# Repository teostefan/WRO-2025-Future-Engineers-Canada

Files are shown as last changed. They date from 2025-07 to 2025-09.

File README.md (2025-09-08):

# WRO-2025-Future-Engineers-Canada

The following repository contains the code and technical documentation regarding
the robot created by the CarletonU-uOttawa joint team for the 2025 WRO Future
Engineers competition.

Robot Image

## Contents

- [About our Team](https://github.com/teostefan/WRO-2025-Future-Engineers-Canada/blob/main/README.md#about-our-team)
- [Demo Video](https://github.com/teostefan/WRO-2025-Future-Engineers-Canada/blob/main/README.md#demo-video)
- [Software Setup](https://github.com/teostefan/WRO-2025-Future-Engineers-Canada/blob/main/README.md#software-setup)
- [Power and Sensor Management](https://github.com/teostefan/WRO-2025-Future-Engineers-Canada/blob/main/README.md#power-and-sensor-management)
- [Obstacle Management](https://github.com/teostefan/WRO-2025-Future-Engineers-Canada/blob/main/README.md#obstacle-management)
- [Mobility Management](https://github.com/teostefan/WRO-2025-Future-Engineers-Canada/blob/main/README.md#mobility-management)

## About our Team

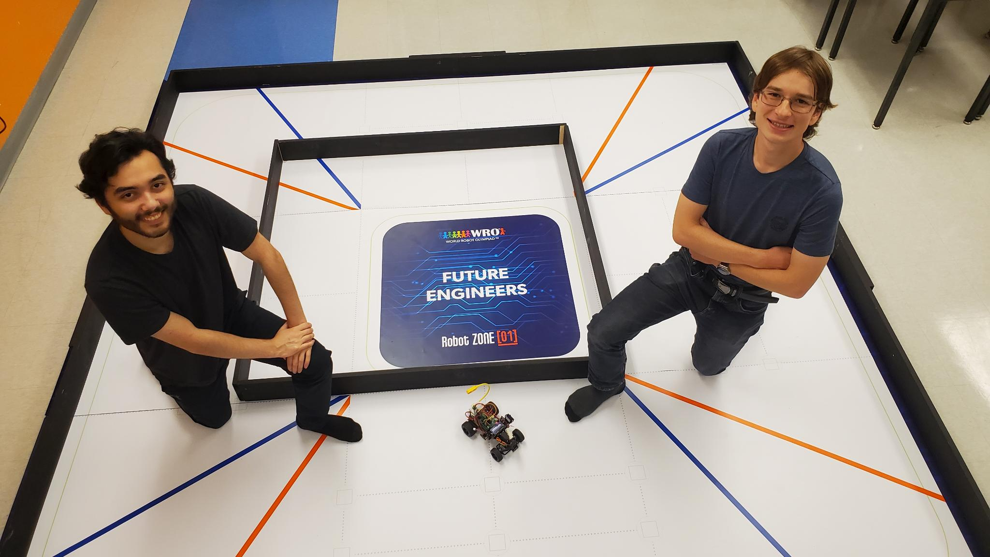
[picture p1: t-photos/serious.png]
Team Photo


Oscar Barbieri is a student at the University of Ottawa and is studying software engineering, and Stefan Teodorescu is a student a Carleton University studying aerospace avionics. Last year, Oscar and Stefan participated in the WRO Future Innovators challenge and made it into the international finals in İzmir. This year, both students have decided to participate in the WRO Future Engineers competition as a means to further their knowledge regarding mechatronics and systems programming.

## Demo Video

A demonstration video of our robot performing both challenges can be found in the [```video``` directory](https://github.com/teostefan/WRO-2025-Future-Engineers-Canada/tree/main/video).

## Software Setup

### Compiling and Running the Robot's Firmware (Linux)

To get started, clone the repository and build the firmware using `make`:

```sh
git clone https://github.com/teostefan/WRO-2025-Future-Engineers-Beta.git
cd WRO-2025-Future-Engineers-Beta
make
```

> **Note**: Depending on how your Linux system is configured, an "insufficient
> privileges" error may be thrown on compilation regarding the file
> `kf_matrix_gen.sh`. To solve this, run
> `sudo chmod 777 ./software/kf/kf_matrix_gen.sh` in the repository's root. If
> this error still persists, use `sudo` in front of `make` as your user might
> not have enough privileges to execute the above bash file.

Then, simply run the `main` executable in the generated `builds` folder:

```sh
builds/main
```

### Compiling and Running Individual Tests

To generate the test executables, run:

```sh
make all-tests
```

Afterwards, all tests will be in the `builds` folder and have a name in the
format `test_xx`. Each test can then be individually executed as in the
following example:

```sh
builds/test_cv
```

### Software Dependencies

If running on Linux, all of the below dependencies should be pre-installed.

- `ffmpeg` - Abstraction layer for the driver, also used for applying filters to
  the video feed.
- `v4l2` - Video4Linux2 multimedia drivers.
- `ffplay` - Media player GUI for debugging.
- `unistd.h` - The UNIX standard header.

## Power and Sensor Management

|Annotated Diagram|
|:--:|
|*Figure 1: Annotated diagram of the vehicle. Individual components are discussed in the subsequent sections.*|

This section pertains to the electrical engineering aspects of our vehicle. Design choices such as computing platforms, power supplies, sensors and motor controllers are discussed. The majority of peripherals have been purchased as breakout boards, and a custom Raspberry-P "Hat" acts as a distribution box and motor controller. A general block diagram of the robot's electrical systems is provided below.

|Drivetrain Diagram|
|:--:|
|*Figure 2: Diagram of the vehicle's electrical systems. Schematics regarding the custom Raspberry Pi Hat PCB and 5V converter for the servo are provided in the sections below.*|

### Computing Platform

The main controller for the robot is a Raspberry Pi 4B Single Board Computer (SBC). All processing is done on this platform, and no additional controllers have been used, except for an ATTINY45 that generates Pulse-Width Modulation (PWM) to control the speed on the driving motor. This ensures that the system remains simple and allows for a smaller vehicle, which implies better manoeuvrability. The Raspberry-Pi model 4B was specifically chosen as it has a good amount of processing capabilities for the computer-vision algorithms and does not excessively consume power like the newer model 5 (~2.5A@5V versus 5A@5V).

### Power Supply

The vehicle is powered by a 2Ah lithium-ion battery pack that feeds 7.4V nominal into a 3.4A fixed 5V buck regulator and a variable 2A buck-boost regulator set to approximately 9V. The 5V regulator supplies the Raspberry Pi, while the 9V regulator supplies the driving motor. As the steering servo requires 5V only, the 9V from the motor power supply is stepped down to 5V via a simple LM7805 linear regulator circuit (see Figure 3). Although the 5V could have been supplied from the main 5V regulator, this would have been undesirable as any electrical noise caused by the servomotor could permeate to the Raspberry Pi and cause instabilities. For supplying the sensors which work at 3.3V, the internal regulator on the Raspberry Pi is used.

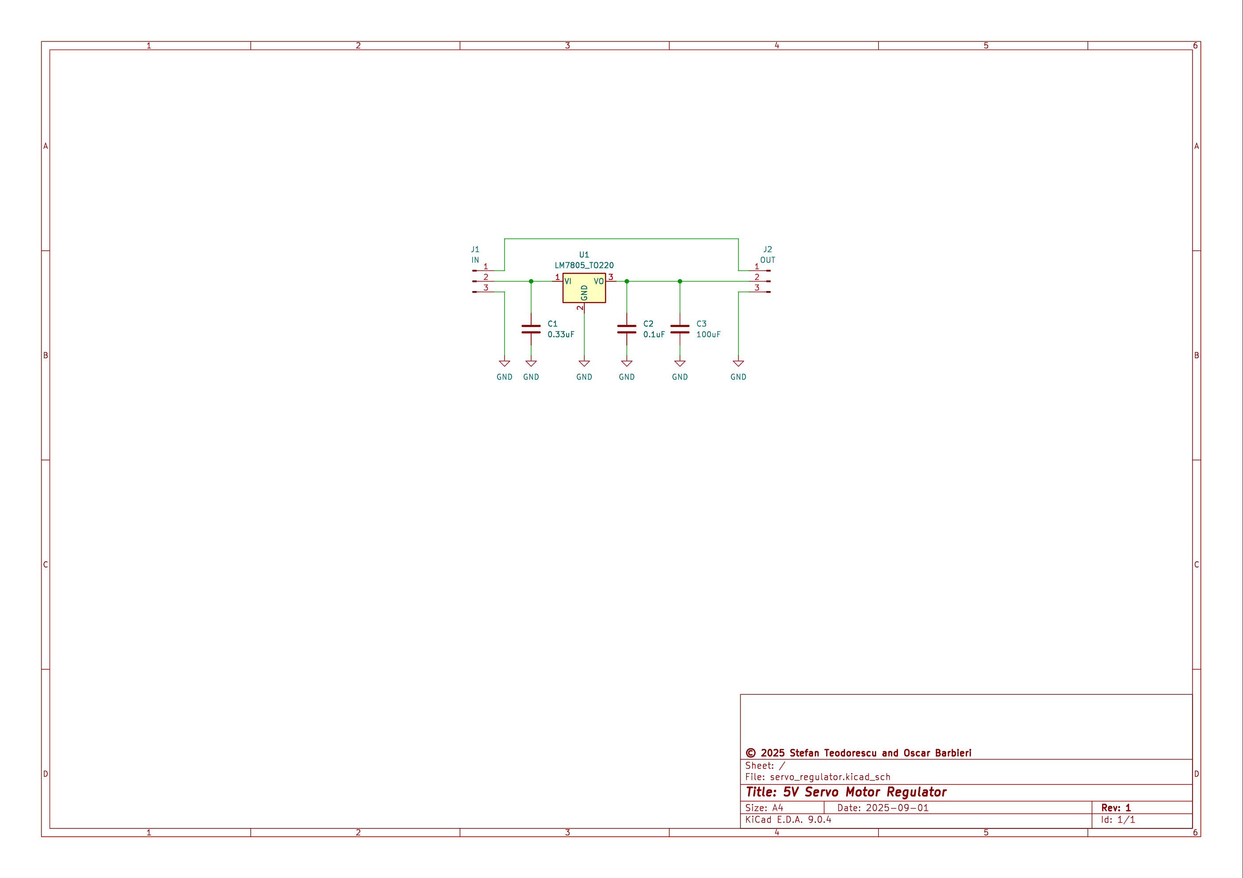
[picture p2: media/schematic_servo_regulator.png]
Servo Regulator Schematic
||
|:--:|
|*Figure 3: Schematic of the LM7805 5V regulator for the steering servo. Production files for this board can be found in the [`pcb/servo_regulator`](https://github.com/teostefan/WRO-2025-Future-Engineers-Canada/tree/main/pcb/servo_regulator) directory.*|

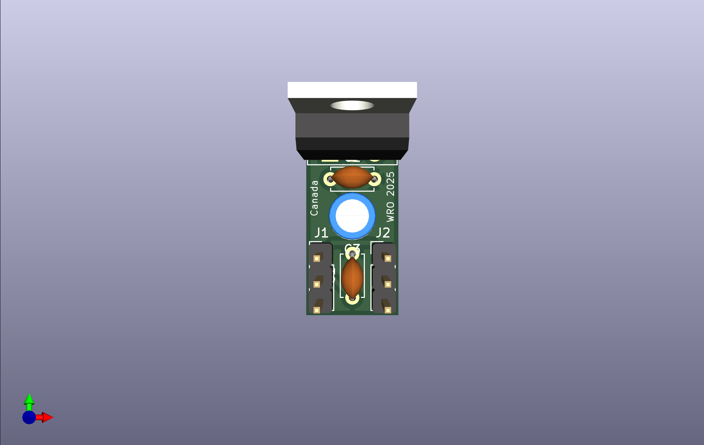
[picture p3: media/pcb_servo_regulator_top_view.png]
Servo Regulator Top View
||
|:--:|
|*Figure 4: Rendering of the servo regulator custom PCB in KiCAD.*|

### Sensor and Motor Management

In addition to the camera for obstacle detection, as many sensors as possible have been installed on the robot to simplify the control algorithms and to avoid estimating data. For example, all four sides of the robot have optical Time-of-Flight (ToF) distance sensors, allowing the vehicle not only to determine it's rectilinear position, but also to measure clearances precisely for manoeuvres such as parallel parking. In addition, a gyroscope has been installed which can measure absolute rotation angles of the robot. The gyro sensor is also used in a proportional controller to keep the robot driving straight when required.

All sensors, except for the camera which is connected via USB, are interfaced via a common I²C bus. To prevent conflicts in between sensors which have the same addresses (the 4 ToF sensors), an I²C-controlled multiplexer is used for connecting the main bus to only one sensor at a time.

Also on this main I²C bus is an ATTINY45 which is configured as a slave. It generates PWM signals that are then used to drive the DC driving motor via an H-bridge at varying speeds in forwards or reverse. The steering servomotor is separate and is controlled directly by the Raspberry Pi through PWM.

In order to reduce the number of external components and keep the wiring relatively manageable, a custom Raspberry Pi "Hat" has been designed. It includes connectors for all of the individual peripherals and integrates the driving motor controller as well as the I²C multiplexer. The circuit board was designed in KiCAD and all relevant files can be found in the `pcb/main` directory. See Figure 5 at the end of this page for the main board's schematic, and the green inset in Figure 2 for the main board's block diagram.

#### I²C Peripheral Mapping

**Note:** All I²C peripherals are on I²C channel 1 (GPIO2/SDA & GPIO3/SCL).

| Peripheral | Description | I²C Address | Related Drivers |
| --- | --- | --- | --- |
| ESC | Electronic speed controller for main motor. It is just an ATTNY25/45 programmed with the firmware contained in the `software/esc/esc.ino` C++ file. GPIO23 is also used by the driver to put this peripheral to sleep. | `0x08` | `software/esc` |
| BNO055 | Gyroscope/IMU. By default, the address of this sensor will be `0x29`, but this will interfere with the ToF sensors. To select the alternate address `0x28`, pull the `ADC` pin on the breakout board low. | `0x28` | `software/gyro` |
| VL53L0X | One of four laser ToF sensors. As all sensors have the same address, they must be selected via the I²C switch (see next row). | `0x29` | `software/tof` |
| TCA9544 | 4 Channel I²C switch / multiplexer for selecting 1 of 4 VL53L0X sensors. | `0x70` | `software/i2cmux` |

#### Non-I²C Peripheral Mapping

| Peripheral | Description | Pin number & GPIO | Related Drivers |
| --- | --- | --- | --- |
| SG-5010 | Standard RC PWM-controlled servo for steering. | `GPIO13/PIN33/PWM1` | `software/esc` |
| KANO Webcam | Gooseneck USB Camera for computer vision. | `USB` | `software/cv` |

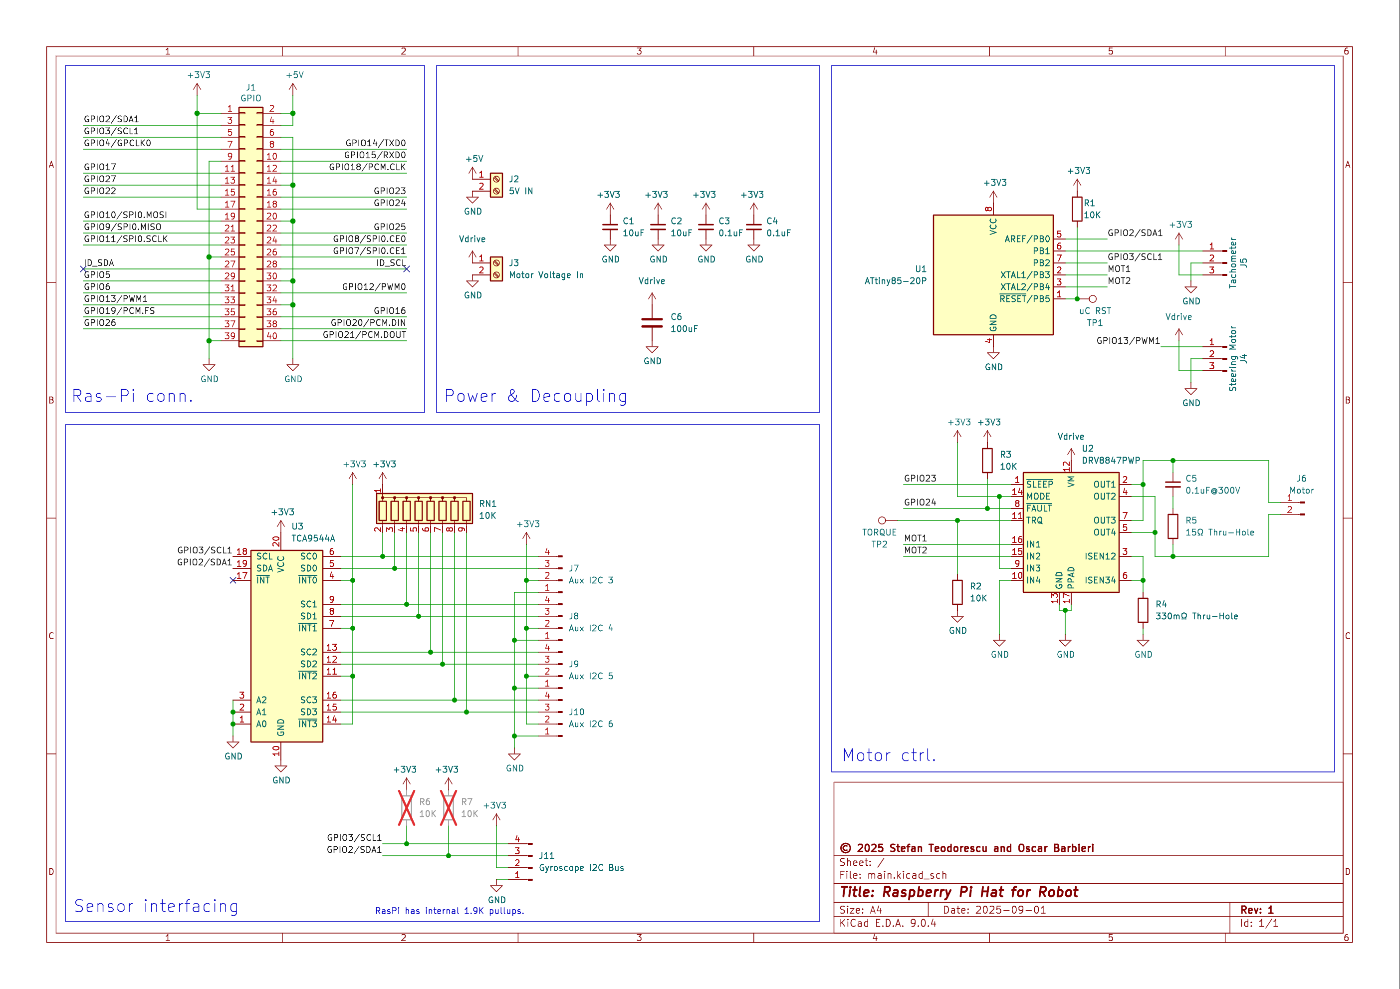
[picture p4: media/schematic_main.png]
Main Board Schematic
||
|:--:|
|*Figure 5: Schematic of the main board. Production files for this board can be found in the [`pcb/main`](https://github.com/teostefan/WRO-2025-Future-Engineers-Canada/tree/main/pcb/main) directory.*|

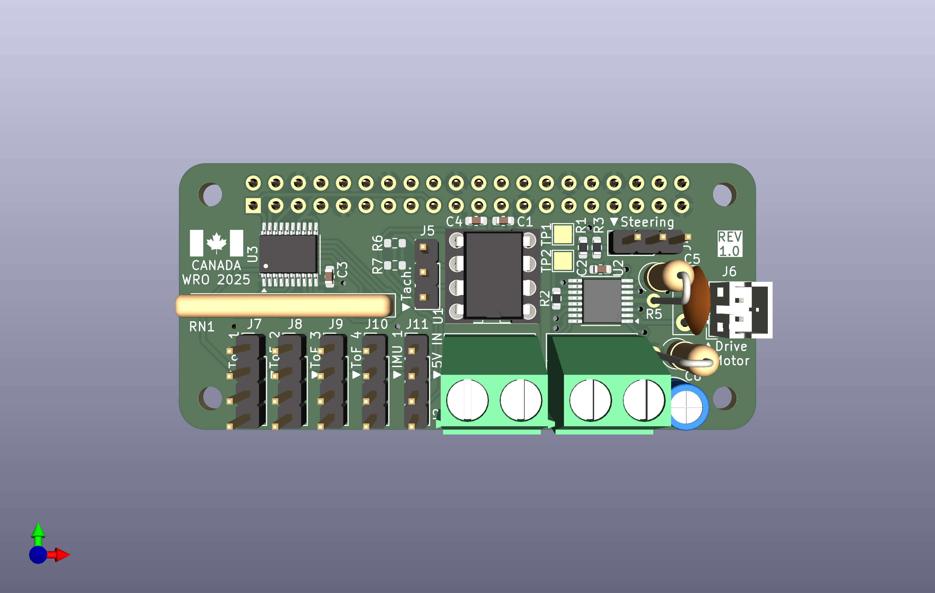
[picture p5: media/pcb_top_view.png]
Main Board Top View
||
|:--:|
|*Figure 6: Rendering of the main board custom PCB in KiCAD.*|

### Bills of Materials

A general Bill of Materials that includes the hardware components as well as the off-the shelf parts can be found at the end of this page. If one desires to fabricate the main board and the servo regulator board, the component-level BOMs can be found in [`pcb/main/main.csv`](https://github.com/teostefan/WRO-2025-Future-Engineers-Canada/tree/main/pcb/main/main.csv) and [`pcb/servo_regulator/servo_regulator.csv`](https://github.com/teostefan/WRO-2025-Future-Engineers-Canada/tree/main/pcb/servo_regulator/servo_regulator.csv).

### Issues faced regarding the sensors

A recurring issue faced during the development of the robot was the instability of the VL53L0X laser time-of-flight sensors (ToF sensors). Despite the [datasheet](https://www.st.com/resource/en/datasheet/vl53l0x.pdf) stating that the performance of the sensor was independent from surface properties, we noticed a very large change in behaviour from when the robot was tested on a black mat versus a glossy white mat like the one used in during the competition. When the ground was highly reflective, the robot would randomly detect walls and behave erratically (see videos below). This occurred whether or not the lights were turned on, suggesting an issue with the sensor's own laser rather than with the ambient light. The effect was also partially corroborated by a [forum post](https://community.st.com/t5/imaging-sensors/vl53l0x-distance-reading-varies-with-reflectivity/td-p/226904) on the manufacturer's website.

<https://github.com/user-attachments/assets/d4aabfce-8ad7-4a68-8b8d-6be23073b4cf>

<https://github.com/user-attachments/assets/641f2a84-3ea8-4779-814c-0cd47e98a4df>

The solution to this issue was to simply have the ToF sensors tilted upwards by 10 degrees with some special 3D printed washers:

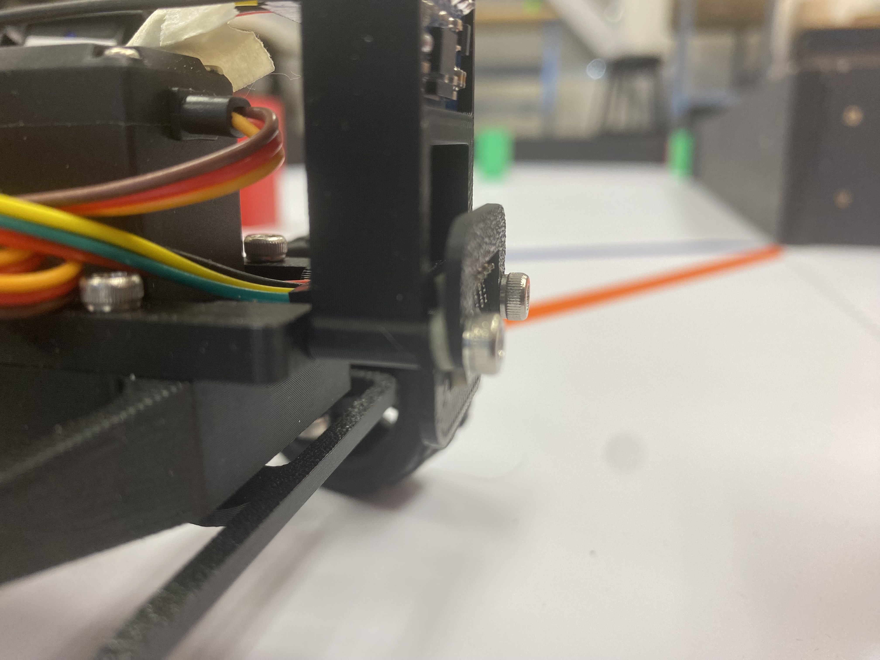
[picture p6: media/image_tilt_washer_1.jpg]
Tilt Washers
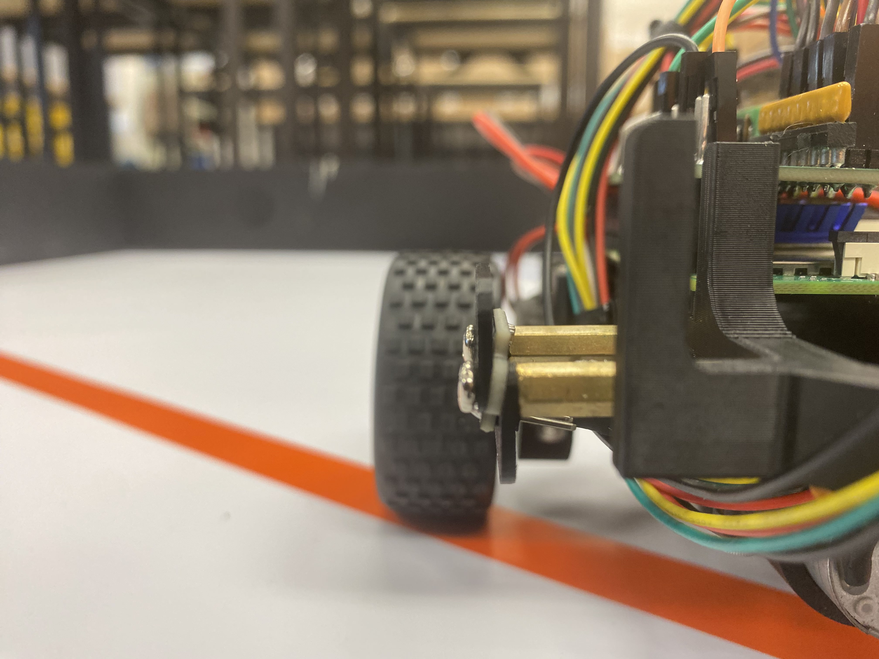
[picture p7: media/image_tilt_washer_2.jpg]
Tilt Washers
|||
|:--:|:--:|
|*Figure 7A: Tilt washers for the front ToF sensor.*|*Figure 7B: Tilt washers for the lateral ToF sensors.*|

This most likely reduced any reflections of the floor coased by the ToF laser's scattering.

## Obstacle Management

For autonomous obstacle avoidance capabilities, the vehicle uses Computer Vision (CV). All software in the vehicle has been written in C, and no premade CV library is used by our code (such as OpenCV). Everything has been written from scratch as a learning experience and to reduce bloat. More details regarding the robot's algorithms is provided below.

### General Algorithm

The following flowchart showcases the robot's behaviour:

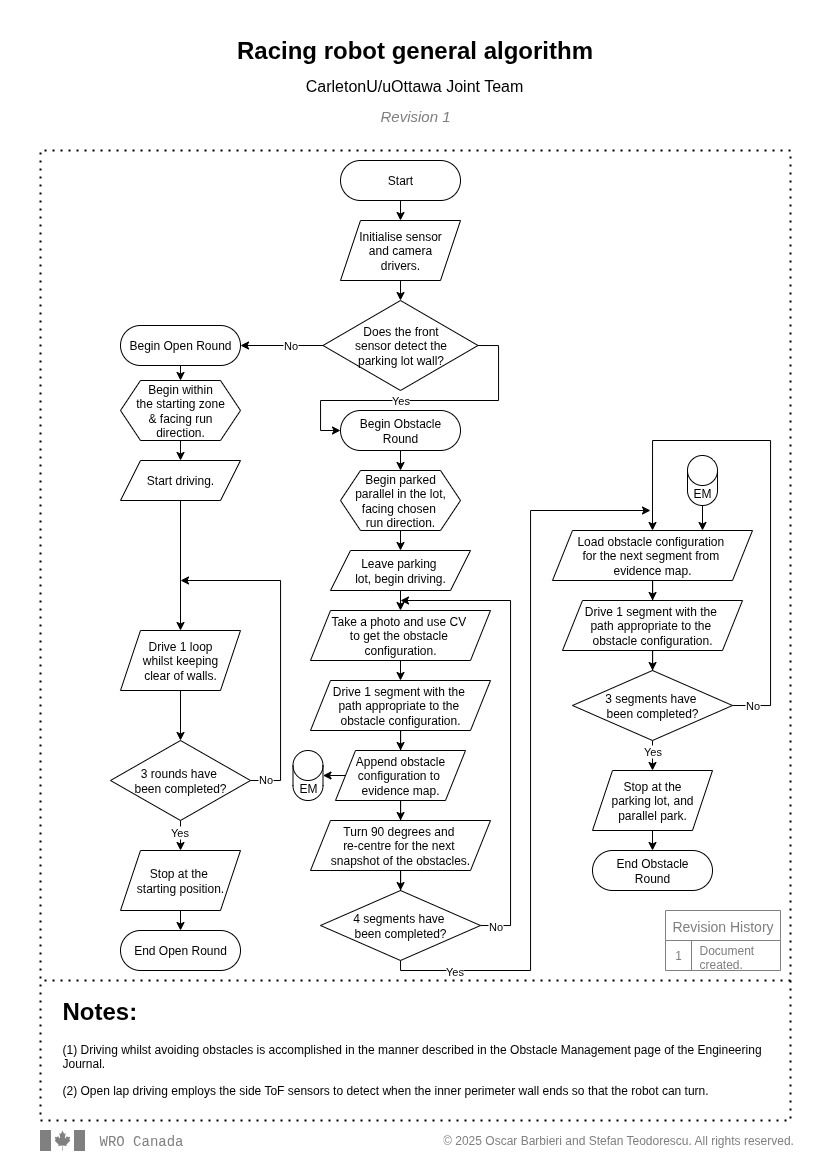
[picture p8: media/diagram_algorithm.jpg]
Algorithm Flowchart
||
|:--:|
|*Figure 8: Flowchart of the robot's software.*|

The open challenge uses the lateral ToF sensors to detect when one of the track sides gives way, indicating the direction in which it should turn. For the obstacle challenge, the computer vision algorithm determines the position of the obstacles for the first round, and then stores all positions into an "evidence map". For the next three rounds, the robot can proceed faster as it uses the stored obstacle position instead of recomputing it from camera data every time.

### Computer Vision

In order to detect and avoid obstacles, the robot centres itself at the beginning of each straight section on the mat to determine the obstacles in it's path. It grabs a frame from the camera, and processes it to figure out the positioning and colour of the obstacles/signs.

|Computer Vision Diagram|
|:--:|
|*Figure 9: Algorithm for the robot's Computer Vision. Relevant code can be found in [```software/cv```](https://github.com/teostefan/WRO-2025-Future-Engineers-Canada/tree/main/software/cv). Obstacle image credit: [WRO Association](https://world-robot-olympiad-association.github.io/future-engineers-gs/p04-cv/).*|

FFMpeg is used as a wrapper for the V4L linux webcam driver to interface with the USB camera and to perform the Gaussian blurring of the image for removing optical noise. The result's pixel data is then piped and stored in a C static array for further processing. Contrast is increased by multiplying each RGB value by 1.5 and then brightness is decreased by subtracting 0.2 from all pixels. This allows bright colours to stand out more and mute fainter colours. Afterwards, the image data is converted from reed-green-blue (RGB) to hue-saturation-luminosity (HSL). A [recursive flood-fill algorithm](https://en.wikipedia.org/wiki/Flood_fill) then subdivides the image into coloured regions by hue, whilst rejecting low saturation and high luminosity regions. While the flood fill algorithm is performed, an accumulator stores the minimum and maximum x and y values for each coloured region to form bounding boxes. Bounding boxes with a minimum dimension less than a threshold are rejected, and the centroids of the remaining bounding boxes are computed. Due to perspective, the y-position of these bounding boxes are used to determine which coloured obstacle is nearer to the robot.

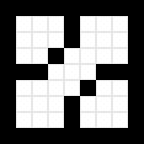
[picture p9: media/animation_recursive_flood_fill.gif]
Flood Fill Demonstration Animation
||
|:--:|
|*Figure 10: A simple animation of the flood fill algorithm. Like coloured connected pixels are traversed to find the minimum and maximum values in x and y of the region. Animation credit: [Wikimedia Commons](https://en.wikipedia.org/wiki/File:Recursive_Flood_Fill_4_(aka).gif)*|

### Obstacle Avoidance

Based on the above Computer Vision algorithm, there are four possible cases returned:

|Case|Obstacle Positioning|
|:--:|:--:|
| 1  | Single RED obstacle |
| 2  | Single GREEN obstacle |
| 3  | RED closer, GREEN further |
| 4  | GREEN closer, RED further |

The exact x positioning of these obstacles is not considered, as the possible x-variation is very small (20cm). Based on these four cases, the robot then chooses one of four paths:

|Case|Diagram of the path taken for the detected obstacle configuration|
|:--:|:--:|
| 1  | Case 1 |
| 2  | Case 2 |
| 3  | Case 3 |
| 4  | Case 4 |

## Mobility Management

The robot and it's linkages/driveshafts are almost fully 3D printed, with only the differential gear being bought off the shelf. All of it's mechanical components were fully designed in IronCAD. This section provides an overview on the decisions regarding the robot's mobility and construction. To see a more in depth overview of the assembly, skip to the [Assembly Instructions](https://github.com/teostefan/WRO-2025-Future-Engineers-Canada/wiki/Mobility-Management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) section on this page.

### Mechanical Design

For mobility, our vehicle uses a rear wheel drive along with front wheel steering. Keeping the steering wheelset separate from the driving wheelset reduces mechanical complexities and removes the need for universal joints in the drive shafts. The powered rear-wheels are connected to the motor via a ring and pinion differential that allows the individual wheel speeds to vary so long as their average is equal to the speed provided by the driving motor. This allows the vehicle to steer efficiently with minimum wheel slippage on the ground. All rotating shafts are connected to the frame through ball-bearings to minimise friction and wear.

|Drivetrain Diagram|
|:--:|
|*Figure 11: Diagram of the vehicle's drivetrain, as seen from the bottom. For an exploded view of all the components, see the vehicle construction section below.*|

### Motors

A brushed Mabuchi RK-370CA-15370 direct-current (DC) motor was chosen for the driving motor as it is easier to control than a brushless motor, requiring only a simple H-bridge circuit instead of a three-phase inverter. The motor's power is regulated through pulse-width modulation.

### Vehicle Construction

The chassis is fully 3D-printed, with files available in the [`hardware` directory](https://github.com/teostefan/WRO-2025-Future-Engineers-Canada/tree/main/hardware) at the root of this repository. The front steering and rear driving are implemented as two separate assemblies which are built individually and then attached together via two beams, forming the structure. The Raspberry-Pi 4 is then screwed into the back and the custom PCB is attached on the 40-pin header. A plate supporting all of the regulators is screwed into the back, while breakout boards for the ToF sensors are attached into the side of the chassis through 20 mm M3 brass standoffs. The front ToF sensor is attached with a special 3D printed bracket that also holds the IMU/Gyroscope breakout. A rack in-between the Raspberry-Pi and the steering motor holds the 2 Ah lithium-ion batteries.

|Front View|Side View|Rear View|
|:--:|:--:|:--:|
|*Figure 12A: Front view of the vehicle.*|*Figure 12B: Side view of the vehicle.*|*Figure 12C: Rear view of the vehicle. See the `v-photos` directory for all six views.*|

### Assembly Instructions and BOMs

A detailed PDF assembly manual has been provided for reference alongside with a BOM for all of the hardware components. Some parts in the BOM must be purchased, while others are to be 3D printed. All 3D printed parts have been made in black Bambu Lab PLA. A seperate BOM for the two custom PCBs are provided in [`pcb/main/main.csv`](https://github.com/teostefan/WRO-2025-Future-Engineers-Canada/tree/main/pcb/main/main.csv) and [`pcb/servo_regulator/servo_regulator.csv`](https://github.com/teostefan/WRO-2025-Future-Engineers-Canada/tree/main/pcb/servo_regulator/servo_regulator.csv).

A preview of the BOM and assembly manual is provided below. For better viewing and to zoom-in, please download the [pdf](https://github.com/teostefan/WRO-2025-Future-Engineers-Canada/blob/main/hardware/Assembly_Manual_and_BOM.pdf).

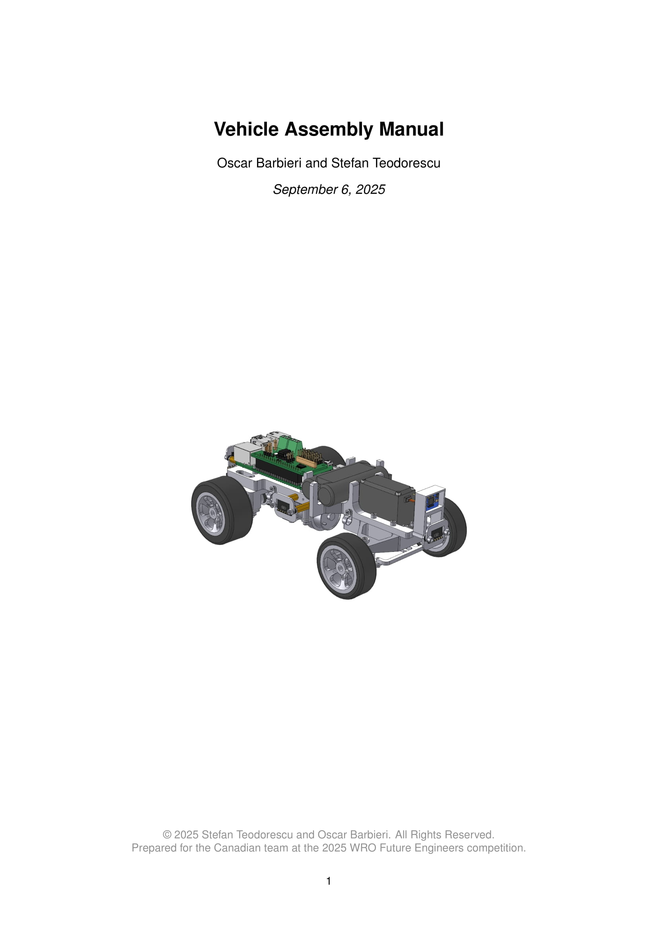
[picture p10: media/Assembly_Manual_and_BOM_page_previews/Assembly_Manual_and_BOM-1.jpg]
Assembly Manual and BOM Page 1


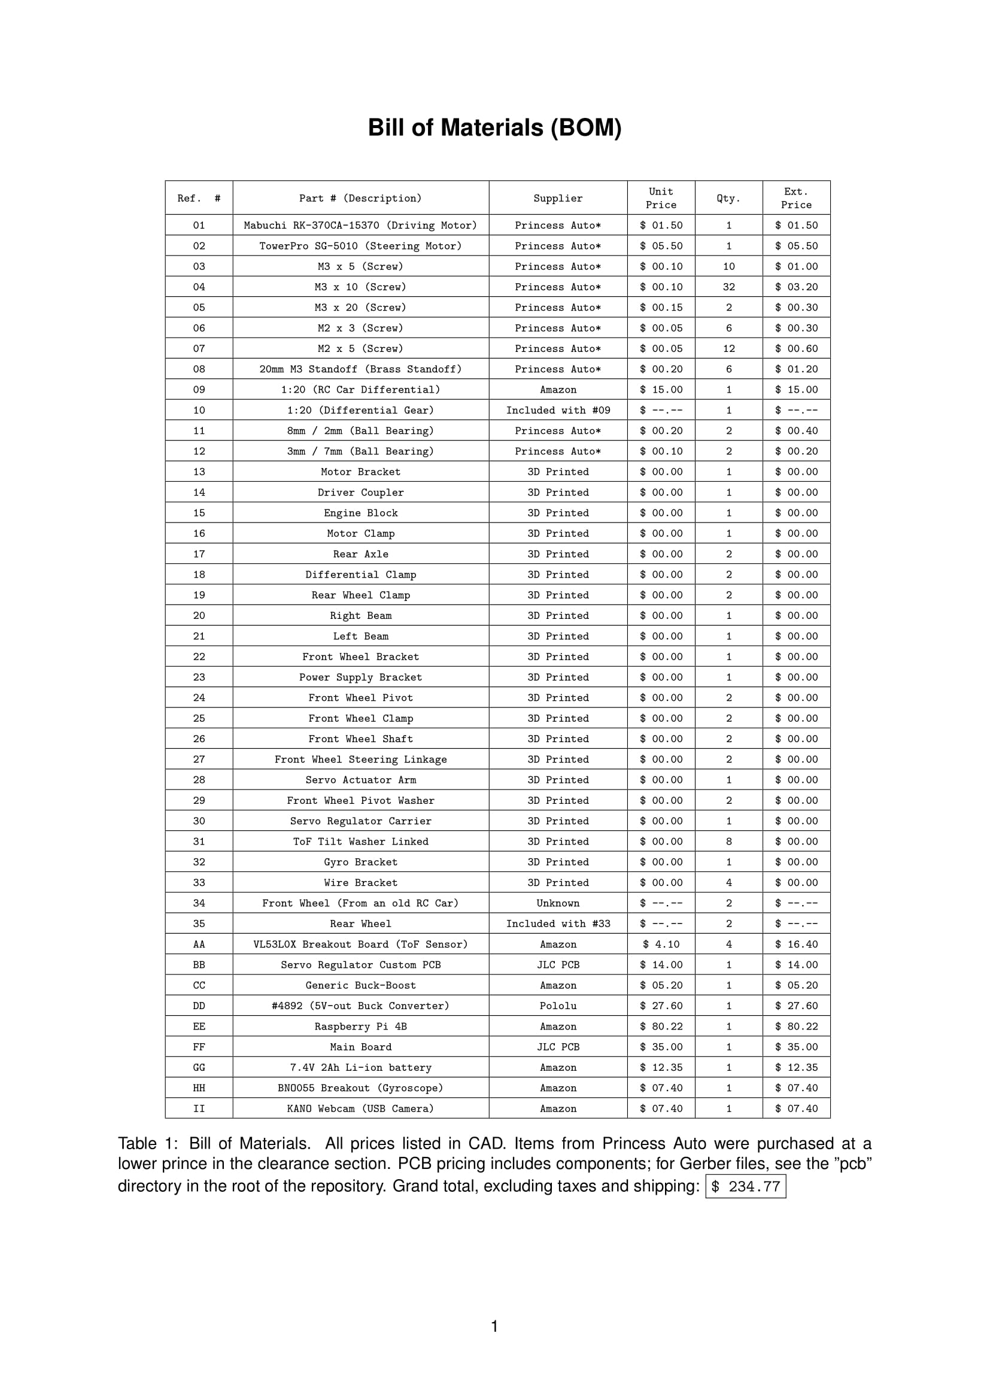
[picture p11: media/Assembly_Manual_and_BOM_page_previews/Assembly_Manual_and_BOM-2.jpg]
Assembly Manual and BOM Page 2


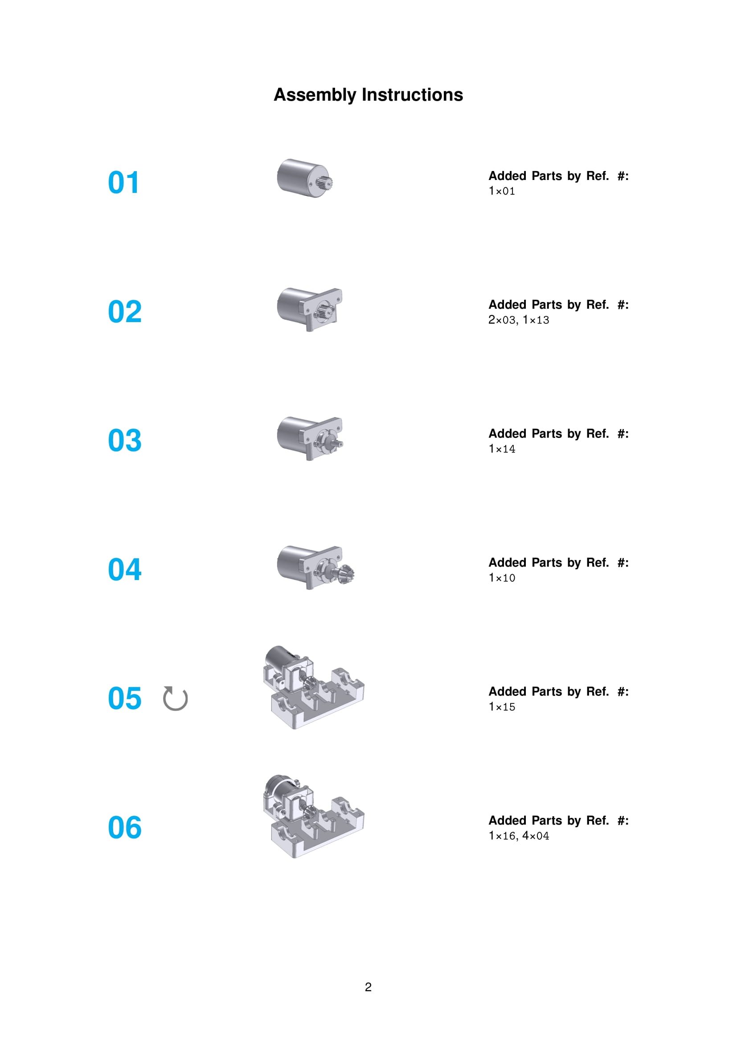
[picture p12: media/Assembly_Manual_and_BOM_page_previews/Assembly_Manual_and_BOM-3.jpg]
Assembly Manual and BOM Page 3


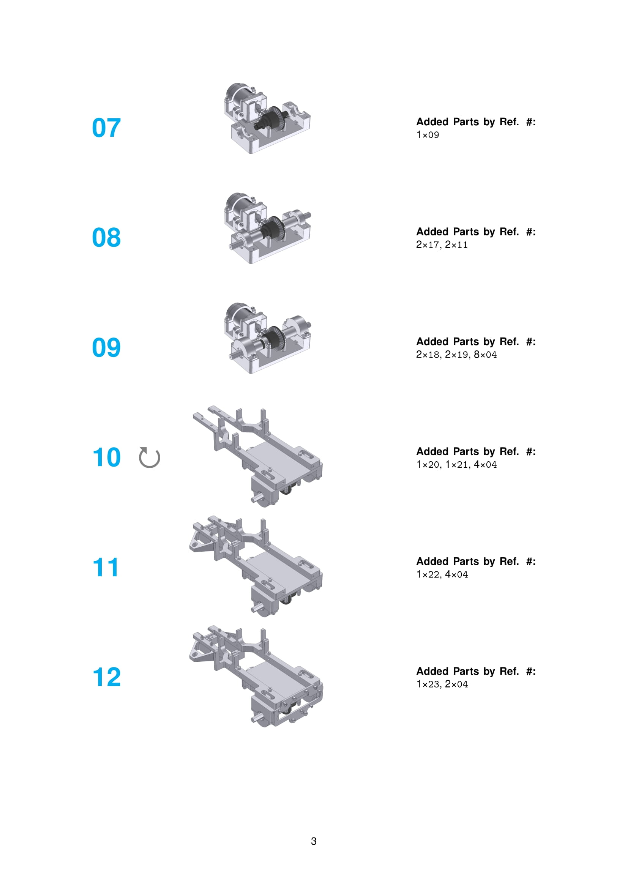
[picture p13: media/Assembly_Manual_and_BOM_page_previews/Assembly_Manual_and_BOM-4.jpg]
Assembly Manual and BOM Page 4


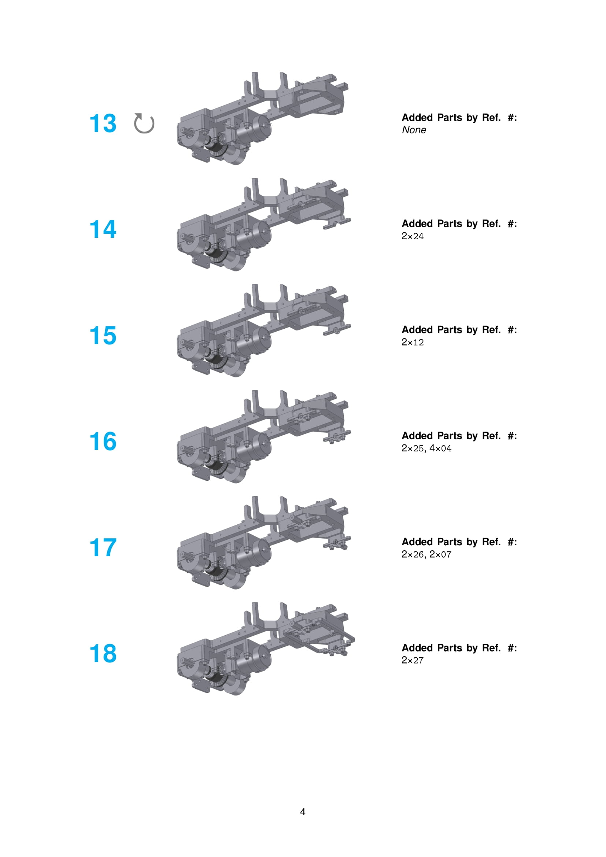
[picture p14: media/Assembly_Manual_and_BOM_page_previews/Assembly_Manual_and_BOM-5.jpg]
Assembly Manual and BOM Page 5


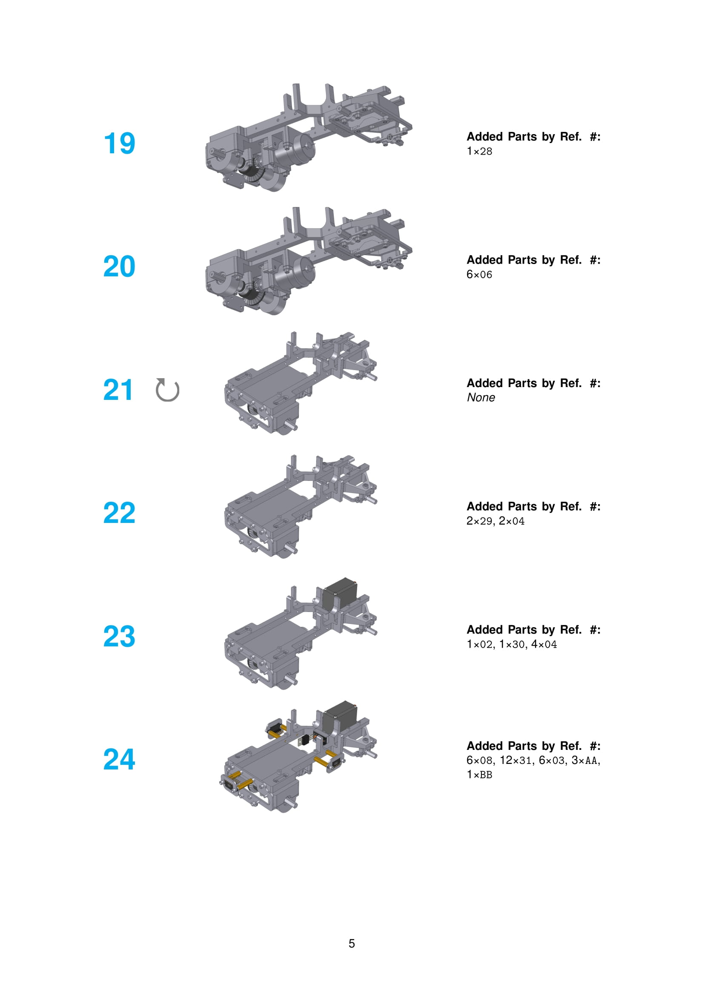
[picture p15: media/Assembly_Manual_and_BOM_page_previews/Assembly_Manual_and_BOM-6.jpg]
Assembly Manual and BOM Page 6


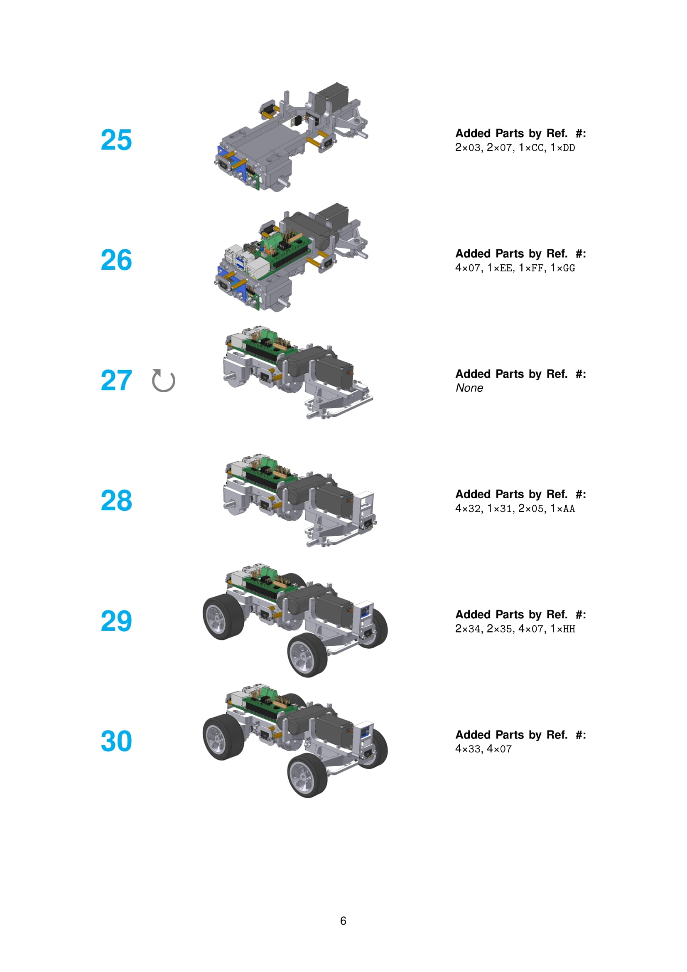
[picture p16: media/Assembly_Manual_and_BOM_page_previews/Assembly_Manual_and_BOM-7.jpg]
Assembly Manual and BOM Page 7


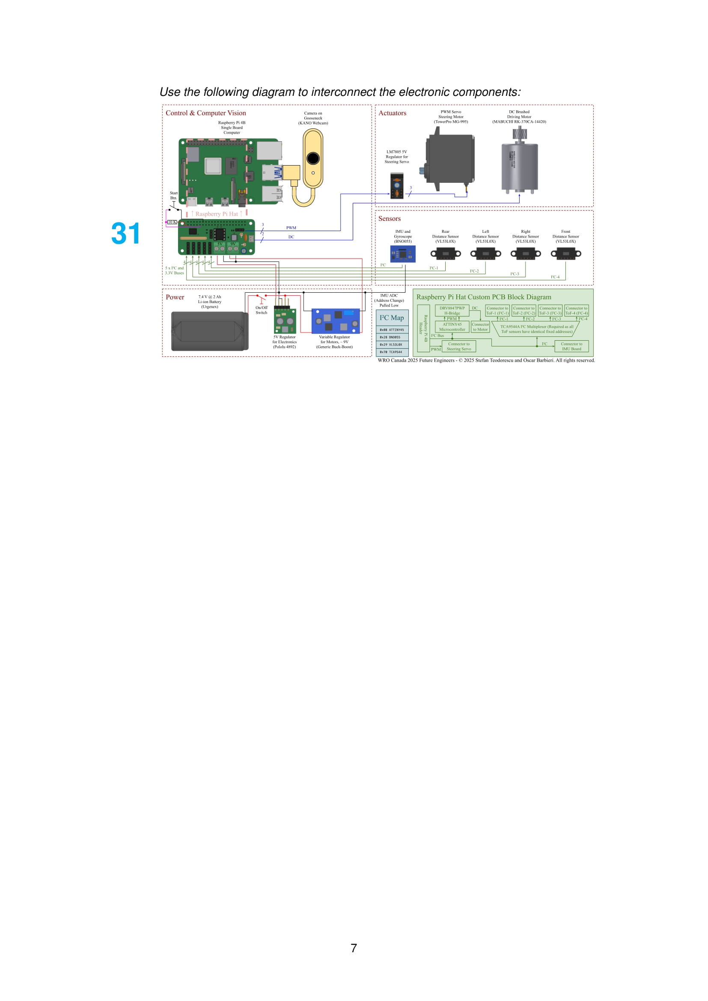
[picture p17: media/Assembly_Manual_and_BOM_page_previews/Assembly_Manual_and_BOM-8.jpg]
Assembly Manual and BOM Page 8


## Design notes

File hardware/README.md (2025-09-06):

In this directory, the IronCAD design files (```WRO2025_final.ics```) as well as an assembly manual and BOM (```Assembly_Manual_and_BOM.pdf```) can be found. The diagrams in the assembly manual are detailed and small, so it is recommended to not have it printed. A PDF viewer should be used so that the document can be zoomed in.

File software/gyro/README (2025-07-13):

# TOF - VL53L0X Time of Flight distance sensor library

This code is based on the Pololu Arduino library (see LICENSE.txt) My aim with this project was to simplify that code and port it to Linux for use on boards like the Raspberry Pi. The problem with ST Micro's part and support software are that they designed their I2C interface specifically to rely on 'magic numbers' for initialization and publish a software library which requires adherance to restrictive licensing terms. By publishing this library, I hope to help more people use the sensor in more ways. The technology and low cost of the sensor make it a valuable addition to the IoT world, but ST Micro's attempt to obfuscate the interface and control the software goes against the open nature of the community.

This code puts the sensor into continous sample mode and allows selection between the default mode (30-800mm) and the long range mode (30-2000mm).

From my limited testing, it appears to give accurate results in the range 40-600mm. Beyond that and the results are less accurate and more prone to being interfered with by ambient light.

**Original repository:** <https://github.com/ZHomeSlice/Simple_BNO055>

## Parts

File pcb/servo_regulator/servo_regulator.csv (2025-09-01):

Reference | Qty | Value | DNP | Exclude from BOM | Exclude from Board | Footprint | Datasheet
C1 | 1 | 0.33uF |  |  |  | Capacitor_THT:C_Disc_D4.7mm_W2.5mm_P5.00mm | ~
C2 | 1 | 0.1uF |  |  |  | Capacitor_THT:C_Disc_D4.7mm_W2.5mm_P5.00mm | ~
C3 | 1 | 100uF |  |  |  | Capacitor_THT:C_Radial_D5.0mm_H5.0mm_P2.00mm | ~
J1 | 1 | IN |  |  |  | Connector_PinHeader_2.54mm:PinHeader_1x03_P2.54mm_Vertical | ~
J2 | 1 | OUT |  |  |  | Connector_PinHeader_2.54mm:PinHeader_1x03_P2.54mm_Vertical | ~
U1 | 1 | LM7805_TO220 |  |  |  | Package_TO_SOT_THT:TO-220-3_Vertical | https://www.onsemi.cn/PowerSolutions/document/MC7800-D.PDF

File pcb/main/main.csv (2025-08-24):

Reference | Value | Datasheet | Footprint | Qty | DNP
C1,C2 | 10uF | ~ | Capacitor_SMD:C_0603_1608Metric | 2
C3,C4 | 0.1uF | ~ | Capacitor_SMD:C_0603_1608Metric | 2
C5 | 0.1uF@300V | ~ | Capacitor_THT:C_Disc_D7.5mm_W2.5mm_P5.00mm | 1
C6 | 100uF | ~ | Capacitor_THT:C_Radial_D5.0mm_H5.0mm_P2.00mm | 1
J1 | GPIO | ~ | Connector_PinSocket_2.54mm:PinSocket_2x20_P2.54mm_Vertical | 1
J2 | 5V IN | https://mm.digikey.com/Volume0/opasdata/d220001/medias/docus/909/1935161.pdf | TerminalBlock_Phoenix:TerminalBlock_Phoenix_MKDS-1,5-2_1x02_P5.00mm_Horizontal | 1
J3 | Motor Voltage In | https://mm.digikey.com/Volume0/opasdata/d220001/medias/docus/909/1935161.pdf | TerminalBlock_Phoenix:TerminalBlock_Phoenix_MKDS-1,5-2_1x02_P5.00mm_Horizontal | 1
J4 | Steering Motor | ~ | Connector_PinHeader_2.54mm:PinHeader_1x03_P2.54mm_Vertical | 1
J5 | Tachometer | ~ | Connector_PinHeader_2.54mm:PinHeader_1x03_P2.54mm_Vertical | 1
J6 | Motor | ~ | Connector_JST:JST_PH_B2B-PH-K_1x02_P2.00mm_Vertical | 1
J7 | Aux I2C 3 | ~ | Connector_PinHeader_2.54mm:PinHeader_1x04_P2.54mm_Vertical | 1
J8 | Aux I2C 4 | ~ | Connector_PinHeader_2.54mm:PinHeader_1x04_P2.54mm_Vertical | 1
J9 | Aux I2C 5 | ~ | Connector_PinHeader_2.54mm:PinHeader_1x04_P2.54mm_Vertical | 1
J10 | Aux I2C 6 | ~ | Connector_PinHeader_2.54mm:PinHeader_1x04_P2.54mm_Vertical | 1
J11 | Gyroscope I2C Bus | ~ | Connector_PinHeader_2.54mm:PinHeader_1x04_P2.54mm_Vertical | 1
R1,R2,R3,RN1 | 10K | http://www.vishay.com/docs/31509/csc.pdf,~ | Resistor_SMD:R_0603_1608Metric,Resistor_THT:R_Array_SIP9 | 4
R4 | 330mΩ Thru-Hole | ~ | Resistor_THT:R_Axial_DIN0309_L9.0mm_D3.2mm_P2.54mm_Vertical | 1
R5 | 15Ω Thru-Hole | ~ | Resistor_THT:R_Axial_DIN0309_L9.0mm_D3.2mm_P2.54mm_Vertical | 1
R6,R7 | 10K | ~ | Resistor_SMD:R_0603_1608Metric | 2 | DNP
TP1 | uC RST | ~ | TestPoint:TestPoint_Pad_2.0x2.0mm | 1
TP2 | TORQUE | ~ | TestPoint:TestPoint_Pad_2.0x2.0mm | 1
U1 | ATtiny85-20P | http://ww1.microchip.com/downloads/en/DeviceDoc/atmel-2586-avr-8-bit-microcontroller-attiny25-attiny45-attiny85_datasheet.pdf | Package_DIP:DIP-8_W7.62mm_Socket | 1
U2 | DRV8847PWP | https://www.ti.com/lit/ds/symlink/drv8847.pdf | Package_SO:HTSSOP-16-1EP_4.4x5mm_P0.65mm_EP3.4x5mm_Mask2.46x2.31mm_ThermalVias | 1
U3 | TCA9544A | http://www.ti.com/lit/ds/symlink/tca9544a.pdf | Package_SO:TSSOP-20_4.4x6.5mm_P0.65mm | 1

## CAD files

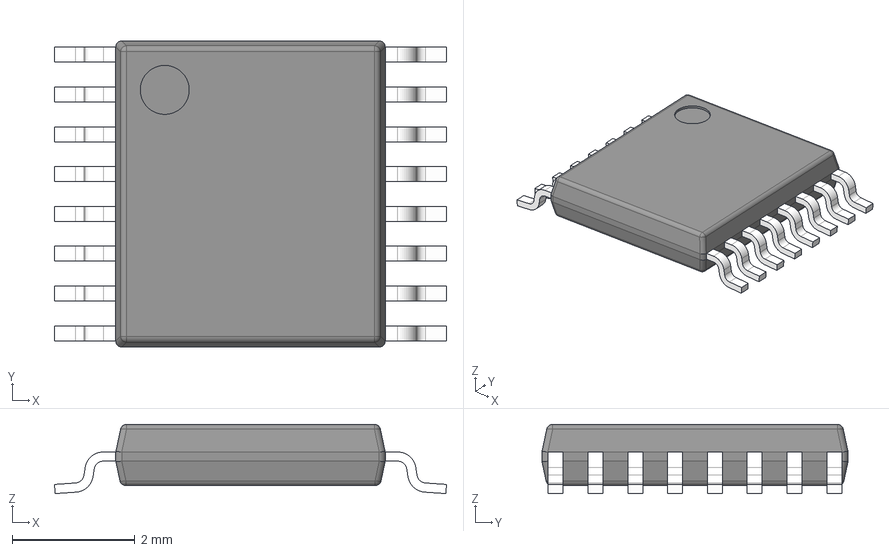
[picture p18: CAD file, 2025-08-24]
pcb/main/drv8847.stp
6.40 x 5.00 x 1.13 mm
BODY-TSSOP
LEAD-TSSOP x 16
PIN1
DAP

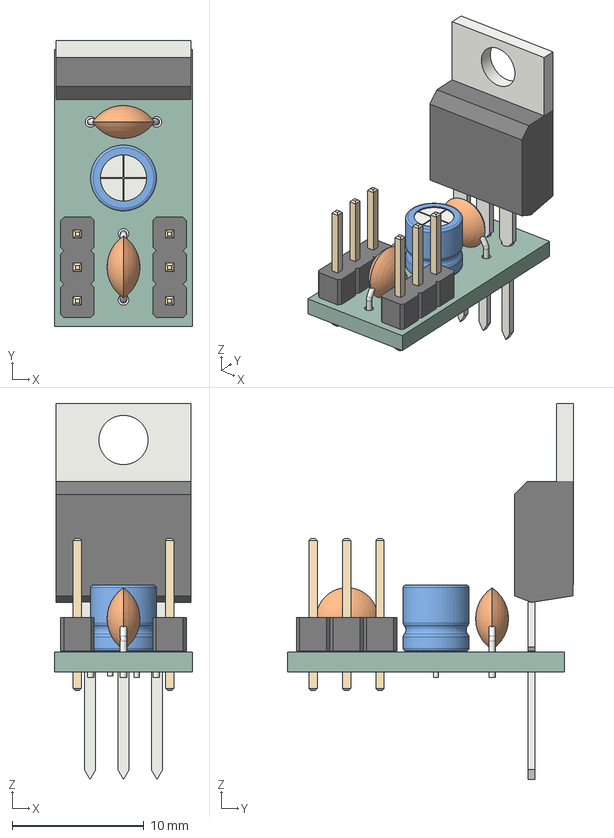
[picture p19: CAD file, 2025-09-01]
pcb/servo_regulator/servo_regulator.step
10.5 x 21.7 x 28.5 mm
C_Radial_D5.0mm_H5.0mm_P2.00mm
TO-220-3_Vertical
C_Disc_D4.7mm_W2.5mm_P5.00mm x 2
PinHeader_1x03_P2.54mm_Vertical x 2
servo_regulator_PCB

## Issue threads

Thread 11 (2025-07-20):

Make PCB

OscarBarbieri, 2025-07-20:
Follow schematic created by @teostefan to produce the PCB (Printed Circuit Board).

teostefan, 2025-07-29:
PCB has been assembled and installed on the robot.

Closed 2025-07-29.

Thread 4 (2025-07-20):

Create Mobility Management Page

OscarBarbieri, 2025-07-20:
Update Mobility Management Page to include all relevant information. Accentuate use of CAD software and hammer home that the robot was constructed primarily of 3D printed materials. Include evidence of the design process.

teostefan, 2025-09-06:
Done.

Closed 2025-09-06.

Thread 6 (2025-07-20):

Create Power and Sense Management Page

OscarBarbieri, 2025-07-20:
Update Power and Sense Management Page to include all relevant information. Explain choice of power source and sensors. Include professional wiring diagrams.

teostefan, 2025-09-06:
Done.

Closed 2025-09-06.

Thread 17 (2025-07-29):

Assemble Electrical Systems

teostefan, 2025-07-29:
Install all PCBs (Raspberry-Pi, interconnects, buck-boost converters & sensors) on the chassis and wire all components together.

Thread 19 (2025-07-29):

Assemble PCB

teostefan, 2025-07-29:
Once the shipment of components arrives in the mail, assemble the custom printed circuit board and perform electrical tests afterwards.

Closed 2025-07-29.

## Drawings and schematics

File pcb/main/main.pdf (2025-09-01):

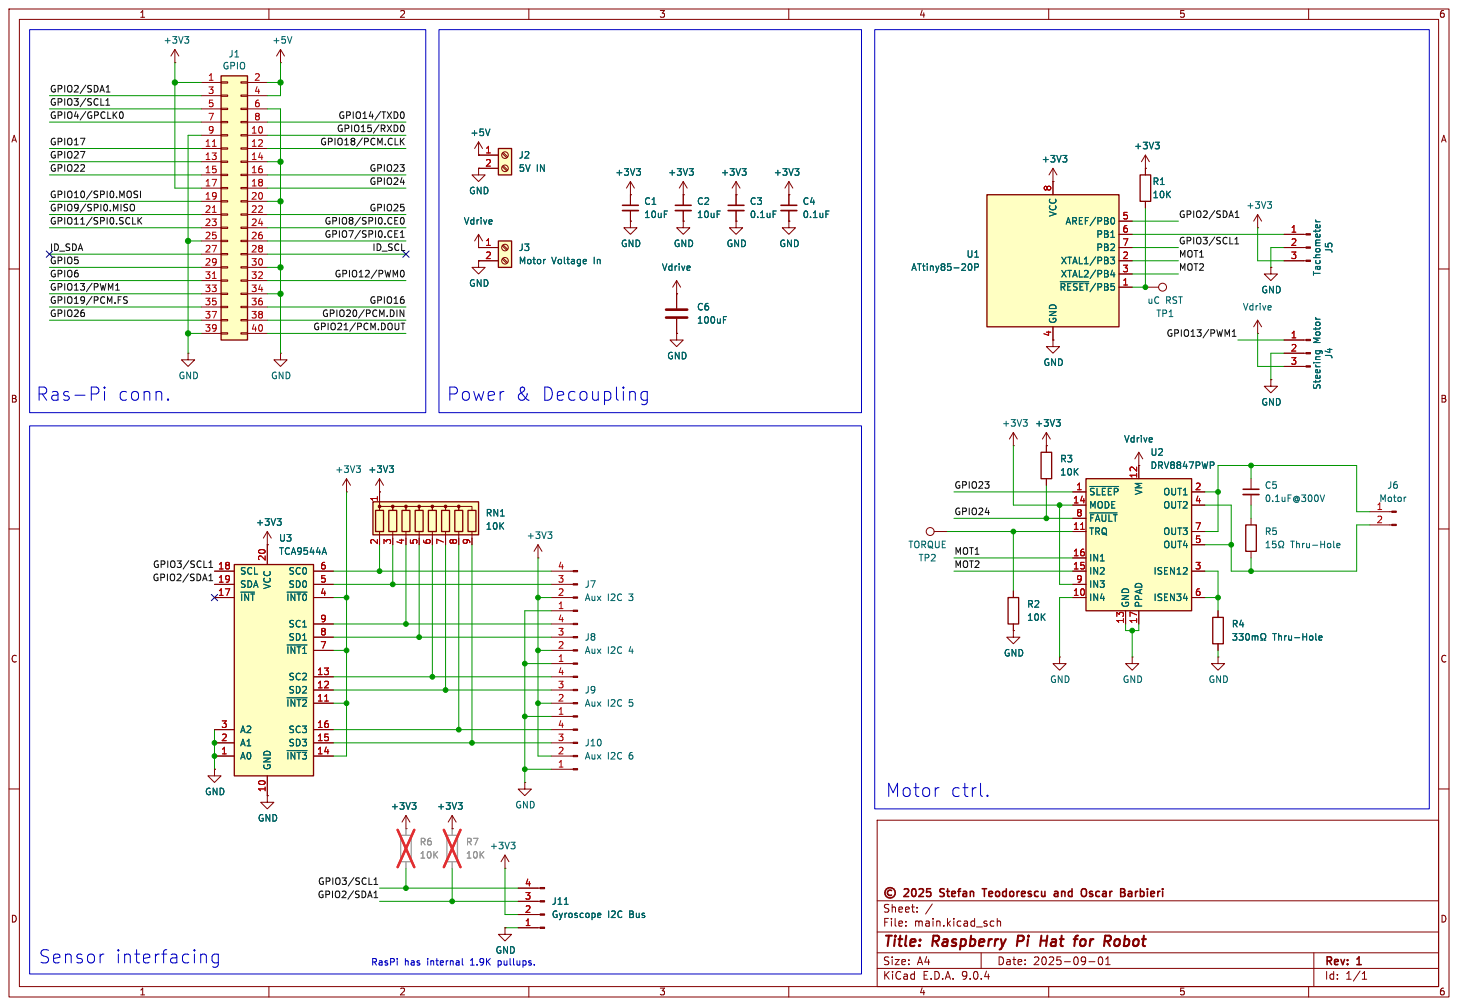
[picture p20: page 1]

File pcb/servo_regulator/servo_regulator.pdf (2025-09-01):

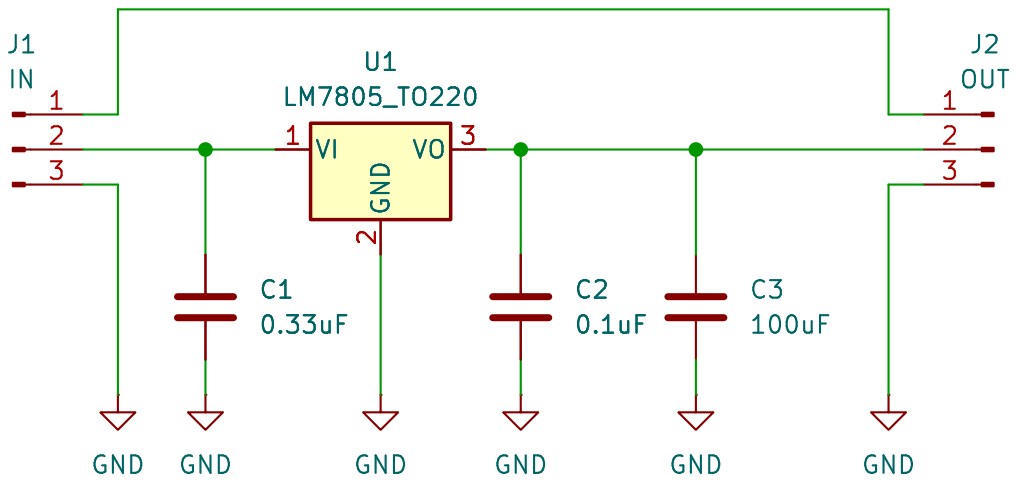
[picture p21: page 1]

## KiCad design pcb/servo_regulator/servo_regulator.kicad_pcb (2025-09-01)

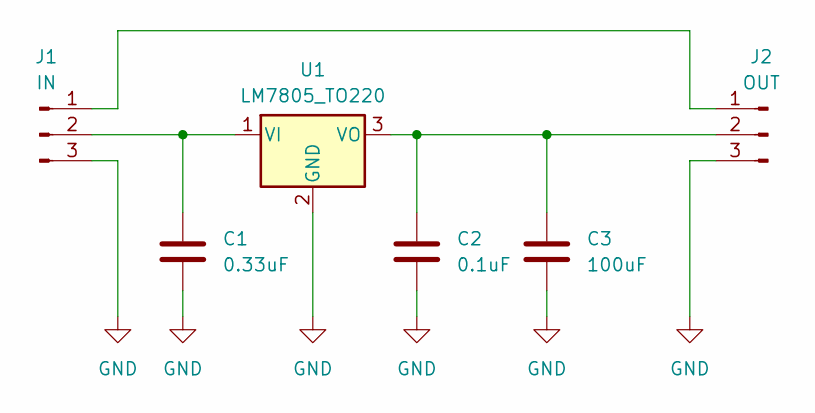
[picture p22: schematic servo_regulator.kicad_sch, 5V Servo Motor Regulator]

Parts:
C1: 0.33uF; C_Disc_D4.7mm_W2.5mm_P5.00mm
C2: 0.1uF; C_Disc_D4.7mm_W2.5mm_P5.00mm
C3: 100uF; C_Radial_D5.0mm_H5.0mm_P2.00mm
J1: IN; PinHeader_1x03_P2.54mm_Vertical
J2: OUT; PinHeader_1x03_P2.54mm_Vertical
U1: LM7805_TO220; TO-220-3_Vertical

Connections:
GND: C1.2, C2.2, C3.2, J1.3, J2.3, U1.2 (GND)
unnamed: J1.1, J2.1
unnamed: C1.1, J1.2, U1.1 (VI)
unnamed: C2.1, C3.1, J2.2, U1.3 (VO)

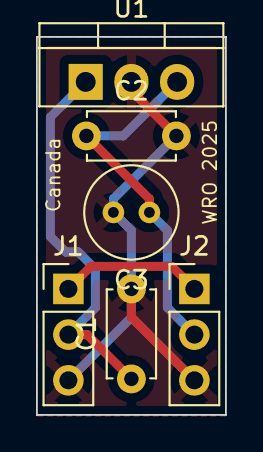
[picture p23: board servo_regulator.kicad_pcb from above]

Board: 2 copper layers, 10.5 x 21.0 mm, 6 parts (0 on the bottom side), 4 nets.

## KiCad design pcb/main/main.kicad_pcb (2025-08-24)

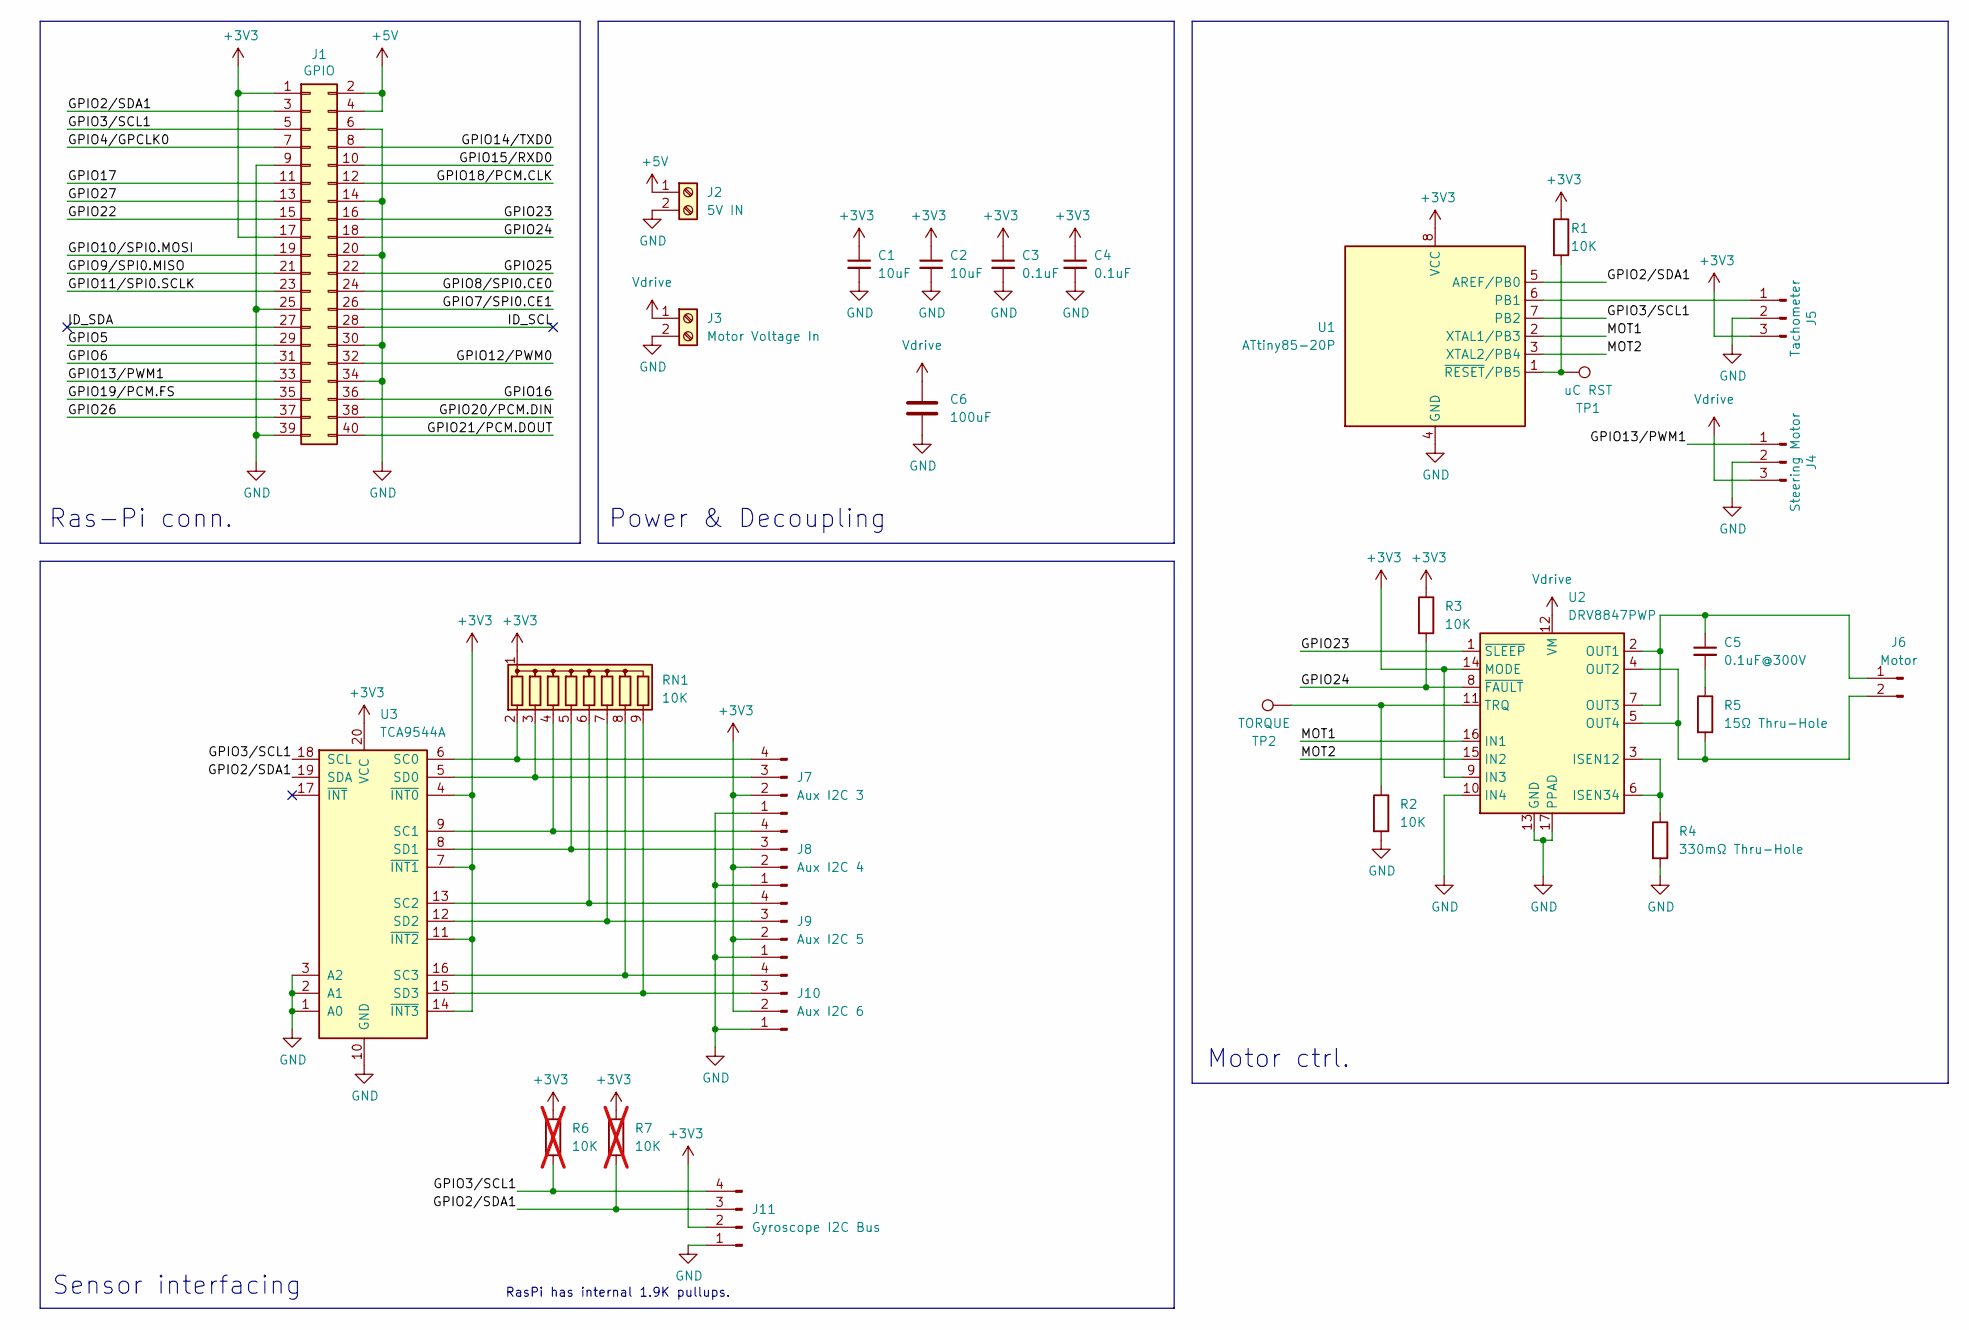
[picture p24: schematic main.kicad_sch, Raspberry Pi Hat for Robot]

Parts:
C1, C2: 10uF; C_0603_1608Metric
C3, C4: 0.1uF; C_0603_1608Metric
C5: 0.1uF@300V; C_Disc_D7.5mm_W2.5mm_P5.00mm
C6: 100uF; C_Radial_D5.0mm_H5.0mm_P2.00mm
J1: GPIO; PinSocket_2x20_P2.54mm_Vertical
J2: 5V IN; TerminalBlock_Phoenix_MKDS-1,5-2_1x02_P5.00mm_Horizontal
J3: Motor Voltage In; TerminalBlock_Phoenix_MKDS-1,5-2_1x02_P5.00mm_Horizontal
J4: Steering Motor; PinHeader_1x03_P2.54mm_Vertical
J5: Tachometer; PinHeader_1x03_P2.54mm_Vertical
J6: Motor; JST_PH_B2B-PH-K_1x02_P2.00mm_Vertical
J7: Aux I2C 3; PinHeader_1x04_P2.54mm_Vertical
J8: Aux I2C 4; PinHeader_1x04_P2.54mm_Vertical
J9: Aux I2C 5; PinHeader_1x04_P2.54mm_Vertical
J10: Aux I2C 6; PinHeader_1x04_P2.54mm_Vertical
J11: Gyroscope I2C Bus; PinHeader_1x04_P2.54mm_Vertical
R1, R2, R3: 10K; R_0603_1608Metric
R4: 330mΩ Thru-Hole; R_Axial_DIN0309_L9.0mm_D3.2mm_P2.54mm_Vertical
R5: 15Ω Thru-Hole; R_Axial_DIN0309_L9.0mm_D3.2mm_P2.54mm_Vertical
R6, R7: 10K; R_0603_1608Metric; not fitted
RN1: 10K; R_Array_SIP9
TP1: uC RST; TestPoint_Pad_2.0x2.0mm
TP2: TORQUE; TestPoint_Pad_2.0x2.0mm
U1: ATtiny85-20P; DIP-8_W7.62mm_Socket
U2: DRV8847PWP; HTSSOP-16-1EP_4.4x5mm_P0.65mm_EP3.4x5mm_Mask2.46x2.31mm_The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
U3: TCA9544A; TSSOP-20_4.4x6.5mm_P0.65mm

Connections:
+3V3: C1.1, C2.1, C3.1, C4.1, J1.1, J1.17, J5.3, J7.2, J8.2, J9.2, J10.2, J11.2, R1.1, R3.1, R6.1, R7.1, RN1.1 (common), U1.8 (VCC), U2.9 (IN3), U2.14 (MODE), U3.4 (~INT0), U3.7 (~INT1), U3.11 (~INT2), U3.14 (~INT3), U3.20 (VCC)
+5V: J1.2, J1.4, J2.1
/GPIO2/SDA1: J1.3, J11.3, R7.2, U1.5 (AREF/PB0), U3.19 (SDA)
/GPIO3/SCL1: J1.5, J11.4, R6.2, U1.7 (PB2), U3.18 (SCL)
/GPIO4/GPCLK0: J1.7
/GPIO5: J1.29
/GPIO6: J1.31
/GPIO7/SPI0.CE1: J1.26
/GPIO8/SPI0.CE0: J1.24
/GPIO9/SPI0.MISO: J1.21
/GPIO10/SPI0.MOSI: J1.19
/GPIO11/SPI0.SCLK: J1.23
/GPIO12/PWM0: J1.32
/GPIO13/PWM1: J1.33, J4.1
/GPIO14/TXD0: J1.8
/GPIO15/RXD0: J1.10
/GPIO16: J1.36
/GPIO17: J1.11
/GPIO18/PCM.CLK: J1.12
/GPIO19/PCM.FS: J1.35
/GPIO20/PCM.DIN: J1.38
/GPIO21/PCM.DOUT: J1.40
/GPIO22: J1.15
/GPIO23: J1.16, U2.1 (~SLEEP)
/GPIO24: J1.18, R3.2, U2.8 (~FAULT)
/GPIO25: J1.22
/GPIO26: J1.37
/GPIO27: J1.13
/ID_SCL: J1.28
/ID_SDA: J1.27
/MOT1: U1.2 (XTAL1/PB3), U2.16 (IN1)
/MOT2: U1.3 (XTAL2/PB4), U2.15 (IN2)
GND: C1.2, C2.2, C3.2, C4.2, C6.2, J1.6, J1.9, J1.14, J1.20, J1.25, J1.30, J1.34, J1.39, J2.2, J3.2, J4.2, J5.2, J7.1, J8.1, J9.1, J10.1, J11.1, R2.2, R4.2, U1.4 (GND), U2.10 (IN4), U2.13 (GND), U2.17 (PPAD), U3.1 (A0), U3.2 (A1), U3.3 (A2), U3.10 (GND)
unnamed: C5.2, R5.1
unnamed: J5.1, U1.6 (PB1)
unnamed: C5.1, J6.1, U2.2 (OUT1), U2.7 (OUT3)
unnamed: J6.2, R5.2, U2.4 (OUT2), U2.5 (OUT4)
unnamed: J7.3, RN1.3 (R2), U3.5 (SD0)
unnamed: J7.4, RN1.2 (R1), U3.6 (SC0)
unnamed: J8.3, RN1.5 (R4), U3.8 (SD1)
unnamed: J8.4, RN1.4 (R3), U3.9 (SC1)
unnamed: J9.3, RN1.7 (R6), U3.12 (SD2)
unnamed: J9.4, RN1.6 (R5), U3.13 (SC2)
unnamed: J10.3, RN1.9 (R8), U3.15 (SD3)
unnamed: J10.4, RN1.8 (R7), U3.16 (SC3)
unnamed: R1.2, TP1.1, U1.1 (~RESET/PB5)
unnamed: R4.1, U2.3 (ISEN12), U2.6 (ISEN34)
unnamed: R2.1, TP2.1, U2.11 (TRQ)
Vdrive: C6.1, J3.1, J4.3, U2.12 (VM)

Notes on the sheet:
Motor ctrl.
Sensor interfacing
Ras-Pi conn.
RasPi has internal 1.9K pullups.
Power & Decoupling

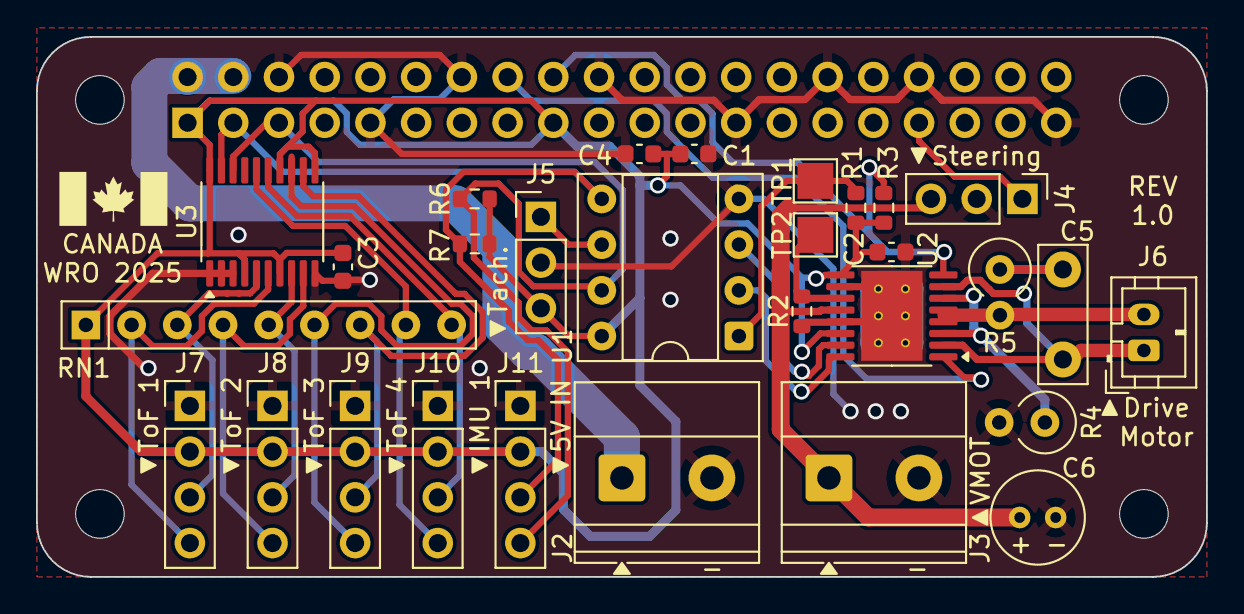
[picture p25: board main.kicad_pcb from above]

Board: 2 copper layers, 65.0 x 30.0 mm, 34 parts (1 on the bottom side), 26 nets.

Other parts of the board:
MH1, MH2, MH3, MH4: MountingHole_2.7mm_M2.5

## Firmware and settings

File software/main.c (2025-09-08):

#ifndef MAIN_C
#define MAIN_C

#include "globals.h"
#include "manoeuvres.c"

int main() {
    // calibrate sensors
    popen("i2cdetect -y 1", "r");
    for (int i = 0; i < 4; i++) {
        i2cmux_switch(i);
        usleep(50000); // 50ms
        tofInit(1, 0x29, 1);
        usleep(50000); // 50ms
    }

    sleep(2);

    BNO_init_i2cbus();
    usleep(50000); // 50ms

    do {
        if (BNO_get_eul(&angles) == -1) {
            printf("An error occurred.");
        }
        printf("Zero Heading = %f degrees ", angles.eul_head);
        zeroHeading = angles.eul_head;
        usleep(50000); // 50ms
    } while (zeroHeading < 1 || zeroHeading > 360);

    esc_enable();
    esc_servo_init();
    esc_servo_steer(0);
    esc_coast();

    do {
        i2cmux_switch(FRONT_MUX);
        usleep(50000); // 50ms
        int frontDistance = tofReadDistance();
        usleep(50000); // 50ms
        i2cmux_switch(REAR_MUX);
        usleep(50000); // 50ms
        int rearDistance = tofReadDistance();
        usleep(50000); // 50ms

        if (frontDistance <= SEE_WALL_DISTANCE && rearDistance <= SEE_WALL_DISTANCE) {
            challenge = challenge;
        } else if (frontDistance >= SEE_WALL_DISTANCE && rearDistance >= SEE_WALL_DISTANCE) {
            challenge = COUNTERCLOCKWISE;
        }
    } while ((frontDistance > SEE_WALL_DISTANCE && rearDistance < SEE_WALL_DISTANCE) || (frontDistance <= SEE_WALL_DISTANCE && rearDistance >= SEE_WALL_DISTANCE));

    if (challenge == OPEN) {
        open_challenge(); // see manoeuvres.c for more details
    } else if (challenge == OBSTACLE) {
        obstacle_challenge(); // see manoeuvres.c for more details
    }

    printf("stopping");

    esc_coast();
    sleep(2);
    esc_servo_steer(0);
    sleep(2);
    esc_disable();
    esc_servo_uninit();

    printf("\nthe end.\n");

    return 0;
}

#endif // MAIN_C

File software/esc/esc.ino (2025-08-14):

/*********************************************************\
|                                                         |
| esc.ino                                                 |
|                                                         |
| © 2025 Oscar Barbieri and Stefan Teodorescu.            |
|                                                         |
| This file contains the firmware for the ATTINY25/45/85  |
| microcontroller on the robot's main circuit board.      |
|                                                         |
| For proper compilation on the Arduino IDE, the          |
| following setup has to be used:                         |
|                                                         |
| 1. Copy just this file into an empty directory named    |
|    "esc" without the other C files found in the parent  |
|    directory. Open the file using the Arduino IDE v2.   |
| 2. Install the ATTiny Board Package by David A Mellis.  |
| 3. Set board to "ATtiny25/45/85".                       |
| 4. Set clock to "Internal 8MHz".                        |
| 5. Use Arduino as ISP programmer.                       |
|                                                         |
| This program is small enough to be used on an ATTINY25. |
|                                                         |
\*********************************************************/

#include <USIWire.h> // NOLINT: Ignore this warning as the code will be compiled with Arduino IDE.

#define HI_NIBBLE(b) (((b) >> 4) & 0x0F) // Get upper nibble from byte. Ex.: 0x36 -> 0x03
#define LO_NIBBLE(b) ((b) & 0x0F)        // Get lower nibble from byte. Ex.: 0x36 -> 0x06.
#define DBL_NIBBLE(n) ((n << 4) | n)     // Duplicate a nibble to form a byte. Ex.: 0x03 -> 0x33.

#define SLAVE_ADDRESS 0x08

#define MOT_A 3
#define MOT_B 4

void setup() {
    pinMode(MOT_A, OUTPUT);
    pinMode(MOT_B, OUTPUT);

    Wire.begin(SLAVE_ADDRESS);
    Wire.onReceive(receiveData);
    Wire.onRequest(sendData);
    // The next section was inspired from http://www.technoblogy.com/show?LE0=:
    TCCR1 = 1 << CTC1 | 1 << PWM1A | 3 << COM1A0 | 7 << CS10;
    GTCCR = 1 << PWM1B | 3 << COM1B0;
    // Interrupts on OC1A match and overflow
    TIMSK = TIMSK | 1 << OCIE1A | 1 << TOIE1;
}

ISR(TIMER1_COMPA_vect) {
    if (!bitRead(TIFR, TOV1)) bitSet(PORTB, MOT_A);
}

ISR(TIMER1_OVF_vect) {
    bitClear(PORTB, MOT_A);
}

void loop() {
}

void receiveData(int bytecount) { // Event when an I²C write is recieved.
    // Control byte format is as follows: xxxxyyyy where xxxx and yyyy are nibbles from 0 to 15 representing
    // the duty cycle for driving the H-bridge channels IN1 (xxxx) and IN2 (yyyy).
    if (bytecount != 1) return;

    char bytein = Wire.read();
    OCR1A = DBL_NIBBLE(LO_NIBBLE(bytein));
    OCR1B = DBL_NIBBLE(HI_NIBBLE(bytein));
}

void sendData() { // There is no I²C registers to be read from.
    Wire.write(0x00);
}

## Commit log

2025-07-30 Renamed the BNO055 directory to "gyro" for more consistency
2025-08-03 Testing updates to gyro and tof
2025-08-04 Created i2c mux driver; all ToF sensors tested good.
2025-08-04 Added drivers to interface with the ESC and changed error messages in i2cmux.
    [esc.c, esc.h, esc.ino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]
2025-08-04 Add ESC enable/disable function for H-Bridge and implement steering servo control.
2025-08-06 Fix all motor related issues; all functions have been successfully tested.
    [esc.c, esc.h, test_esc.c]
2025-08-06 Fixed firmware issues in the ATTINY45 microcontroller that resulted in I²C bus desynchronisation by using hardware PWM peripherals instead of emulating PWM through software.
    [esc.ino]
2025-08-06 Added comment to clarify possible pigpio "errors" given by the linter in esc.h
    [esc.h]
2025-08-16 fix makefile and globals
    [globals.h]
2025-08-23 push everything in case it crashes again
    [io.c, main.c]
2025-08-24 Update drivetrain diagram in media
2025-08-24 Add PCB manufacturing files and 3D renders of the PCB
    [drv8847.stp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]
2025-08-24 Add PCB BOM
    [main.csv]
2025-08-29 Got the button working
2025-08-29 Added main board schematic in media folder
2025-08-30 drives three laps with reverse
    [globals.h, gyro.c, main.c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]
2025-08-31 obstacle tight left, obstacle tight right
    [main.c, test_i2cmux.c]
2025-09-01 Added SVG version of the drivetrain diagram
2025-09-01 Added PCB files for the robot
    [drv8847.stp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]
2025-09-01 Updated schematic images
2025-09-01 Added BOM for the servo regulator
    [servo_regulator.csv]
2025-09-06 Added CAD file for the whole vehicle
2025-09-06 Added Assembly Manual and BOM PDF
2025-09-06 Renamed instruction manual to assembly manual for clarity
2025-09-06 Added PDF previews for the assembly manual and BOM
2025-09-06 Added sensor diagram into media
2025-09-07 Added rendering of the servo regulator PCB
2025-09-07 Added videos to media showcasing ToF sensor issues
2025-09-07 Added algorithm flowchart in media

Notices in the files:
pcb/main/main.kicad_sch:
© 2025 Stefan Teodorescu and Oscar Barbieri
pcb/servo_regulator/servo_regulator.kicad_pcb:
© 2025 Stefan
